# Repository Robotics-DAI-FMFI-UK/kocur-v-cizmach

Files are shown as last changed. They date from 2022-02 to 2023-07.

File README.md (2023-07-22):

# kocur-v-cizmach
Cat-like arduino robot with 4 legs

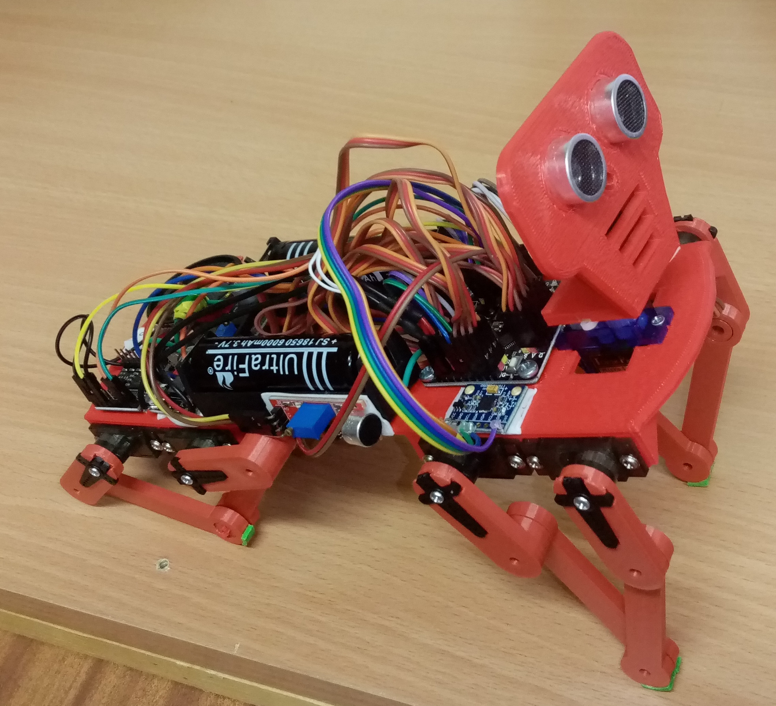
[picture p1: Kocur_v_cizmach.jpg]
kocúr v čižmách


list of parts:

mechanical:

* 4 legs - each made of 4 different pieces
* main body
* head
* screws for fixing arduino, power supply, and battery holders

electronic:

* 2x plastic holder for 16500 LiIon batteries
* 2x 16500 LiIon batteries
* 8x mg90s servo + 1x sg90 or mg90 for head (or 1x continuous servo for new version with rotating front legs)
* arduino nano strong
* lm2596 tuned to 5V (or 2x 5V4A step-down regulator)
* HC-SR04 ultrasonic sensor
* passive buzzer
* KCD-11 power switch
* cables
* resistor divider (i.e. 5.5K + 56K) to measure bat. voltage

optional:

* HC-05 compatible BT module
* extra 5V4A power supply to avoid spurious resets
* DfPlayer Mini, 2W 8Ohm speaker and microSD card
* analog microphone
* mpu6050 gyro/accelerometer
* capacitance touch sensor

Pin connections:

    D0   reserved for programming/serial comm on USB 
    D1   reserved for programming/serial comm on USB 
    D2   BT Tx (i.e. our Rx, signal from BT to Arduino)
    D3   Right back 2 (RB2)
    D4   BT Rx (i.e. our Tx, signal from Arduino to BT)
    D5   Right back 1 (RB1)
    D6   Right front 2 (RF2)
    D7   Right front 1 (RF1)
    D8   Left front 2 (LF2)
    D9   Left front 1 (LF1)
    D10  Left back 1 (LB1)
    D11  Left back 2 (LB2)
    D12  Head
    D13  Buzzer
    A0   US Trig
    A1   US Echo
    A2   DfPlayer Mini Rx
    A3   voltage divider on batteries
    A4   SDA of MPU6050
    A5   SCL of MPU6050
    A6   Touch sensor
    A7   Microphone

Building instructions: https://kempelen.dai.fmph.uniba.sk/files/kocur-v-cizmach-manual/

Choreographies are sequences of motor angles 0-179 8-tuples in this order: (delay is in ms and is applied 100-times per each move, typical values 1-10, e.g. 1 => the movement is spread over 100 steps, each lasting 1ms, in total about 100 ms. To change that parameter, edit play_step() function)

    LF1 LB1 RF1 RB1 LF2 LB2 RF2 RB2 delay

In edit mode, use the following keys to move all degrees of freedom:

   (-> means forward, <- means backward, servo 1 is front, servo 2 back)

    1  LF1 -> -      2  LB1 -> -      3  RF1 -> +      4  RB1 -> +
    q  LF1 <- +      w  LB1 <- +      e  RF1 <- -      r  RB1 <- -
    a  LF2 <- +      s  LB2 -> -      d  RF2 <- -      f  RB2 -> +
    z  LF2 -> -      x  LB2 <- +      c  RF2 -> +      v  RB2 <- -

Kocúr v čižmách (https://www.youtube.com/watch?v=T9AiIFP-OWI)

https://www.youtube.com/watch?v=T9AiIFP-OWI

https://youtu.be/DKM0F1i9IDY

Software:

Arduino program allows to work with "choreographies": create, edit, test and debug, import, export, store into EEPROM, setup autoplay, and control the attached gadgets over the cable or Bluetooth module. Each of the three modes has interactive control and 'h' shows help - list of available commands:

    MoKraRoSA. Press H for help
    Control mode. Hit E for edit mode.
     1: forward
     2: backward
     3: right
     4: left
     5: down
     6: sit
     7: look around
    Play the sequence: /
    Repetitive play: \
    Play eeprom seq: t g b
    Initial position: *
    Position 90: 9
    Ultrasonic ON/OFF: u
    Battery level (*100 V): B
    Play melody: . , ; ' [ ]
    Stop melody: ESC/:
    Play/change music: m j n
    Music volume on/off: M
    Change music volume: < >
    Print help: h
    ---------------------    
    Edit mode. Hit C for control mode.
    Servo control:
    1 ... q
    2 ... w
    e ... 3
    r ... 4
    z ... a
    s ... x
    d ... c
    v ... f
    Step size control:
    - ... +
    Store next point: ENTER/W
    Print the sequence: SPACE/N
    Load (paste in) the sequence: L
    Save to EEPROM: E
    Load from EEPROM: O
    Toggle autostart: A
    Erase sequence: R
    Undo to last saved position: U
    Enter debug mode: TAB/T
    (to insert a break, repeat the same position again with delay)
    Play the sequence: /
    Repetitive play: \
    Play eeprom seq: t g b
    Initial position: *
    Position 90: 9
    Ultrasonic ON/OFF: u
    Battery level (*100 V): B
    Play melody: . , ; ' [ ]
    Stop melody: ESC/:
    Play/change music: m j n
    Music volume on/off: M
    Change music volume: < >
    Print help: h
    ---------------------    
    Debug mode:
     TAB/T   - leave debug mode
     SPACE/N - move to next step
     ENTER/W - replace with current
     ESC/:   - restore current step
     D       - delete current step
     ESC/:   - insert step before current
    Servo control:
    1 ... q
    2 ... w
    e ... 3
    r ... 4
    z ... a
    s ... x
    d ... c
    v ... f
    Step size control:
    - ... +
    Print help: h

Warning:

The LiIon batteries are sensitive to a complete discharge, therefore
the battery voltage is permanently measured using a voltage-divider
against the built-in 1.1V power regulator, and when they reach
a critical level, all functionality stops and an alarm is played
using the passive buzzer. It is recommended to recharge batteries
after the use, and store them for longer term charged to about a half
of their capacity.

Links:

*  Original project that inspired us: Baby “MIT Cheetah” opensource and 3D-printable robot by Marco (https://www.personalrobots.biz/baby-mit-cheetah-opensource-and-3d-printable-robot/)
* Our modifications in TinkerCAD (they may change): body and head (https://www.tinkercad.com/things/c9znID17vLj-cheetah-telo), legs (https://www.tinkercad.com/things/6ybUZ9S300i-cheetah-noha)
* Student project summer 2021: https://dai.fmph.uniba.sk/courses/dtv/index.php/Cheetah
* Student project winter 2021: https://wiki.robotika.sk/robowiki/index.php?title=Kocur_v_Cizmach_-_Alja%C5%BE_Andol%C5%A1ek_and_Ursek_Slivsek

contact: Pavel, pavel.petrovic at uniba.sk

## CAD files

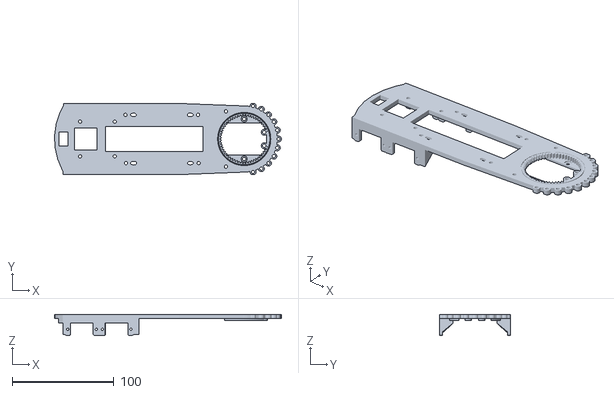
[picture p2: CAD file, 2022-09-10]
stl/v3/cheetah_v3_body_main.stl
223.0 x 70.0 x 20.8

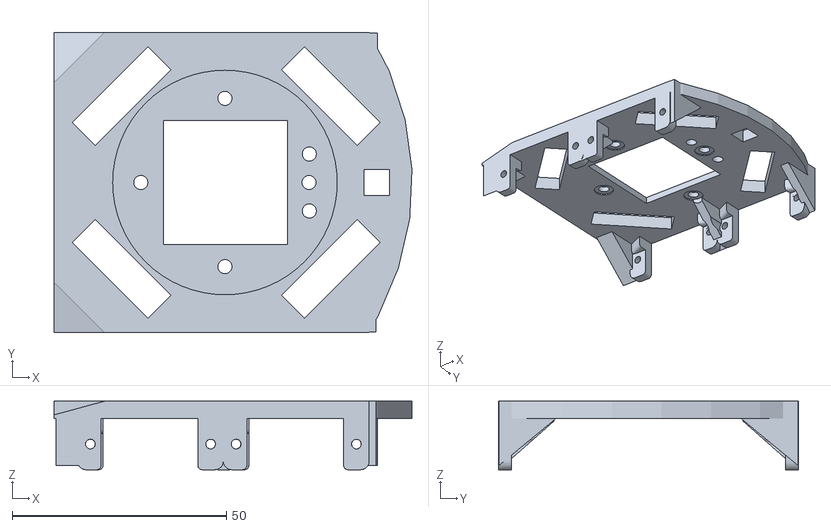
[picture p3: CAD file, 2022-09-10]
stl/v3/cheetah_v3_body_frontlegs_holder.stl
83.5 x 70.0 x 16.0

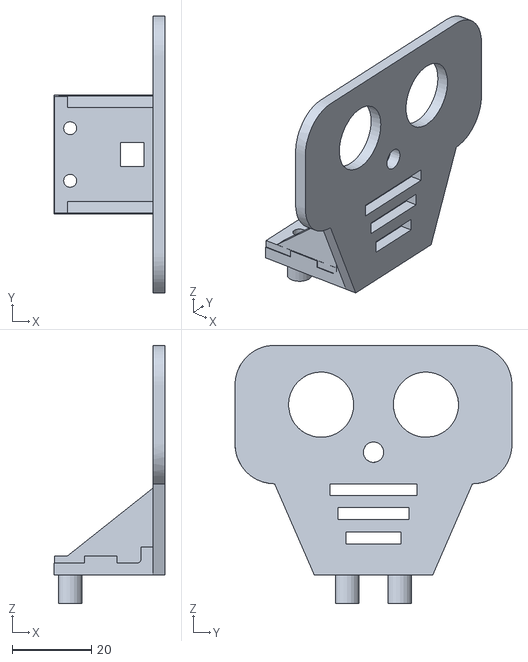
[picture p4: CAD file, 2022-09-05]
stl/v3/cheetah_v3_head.stl
28.0 x 70.0 x 65.3

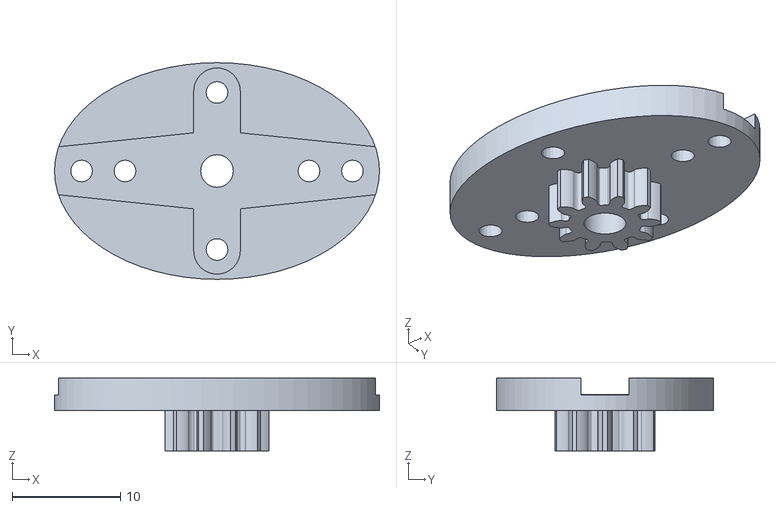
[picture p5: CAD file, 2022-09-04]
stl/v3/cheetah_v3_servo_gear.stl
30.0 x 20.0 x 6.72

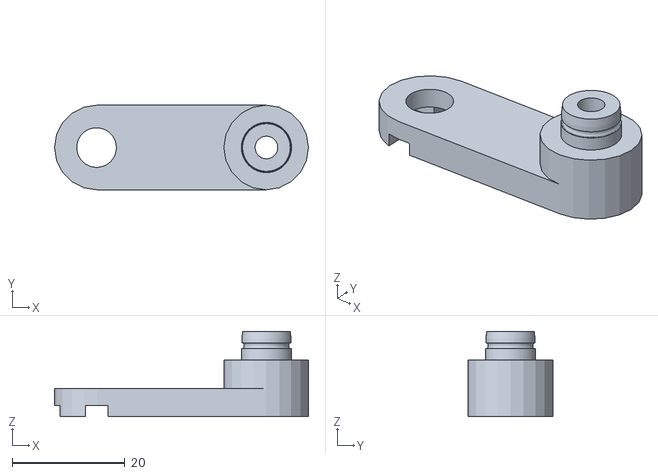
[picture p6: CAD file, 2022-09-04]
stl/v3/cheetah_v3_leg_B.stl
45.0 x 15.0 x 15.1

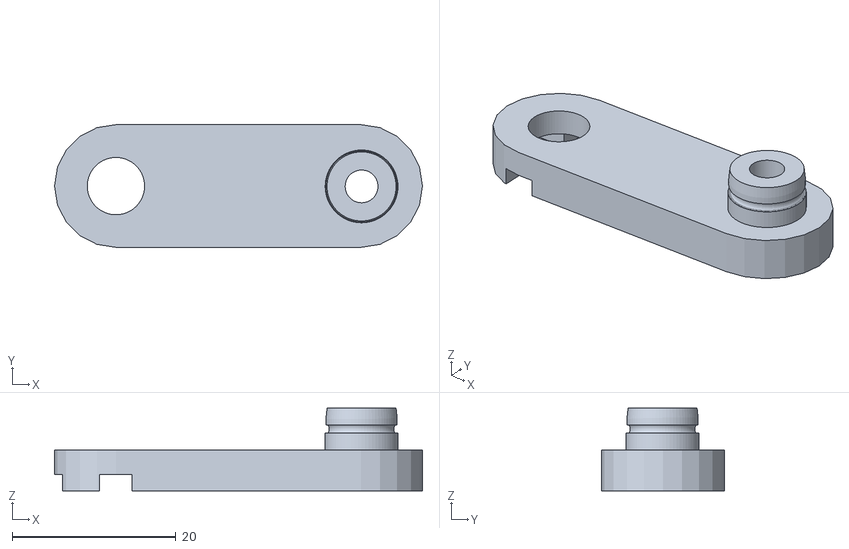
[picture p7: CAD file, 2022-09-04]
stl/v3/cheetah_v3_leg_C.stl
45.0 x 15.0 x 10.1

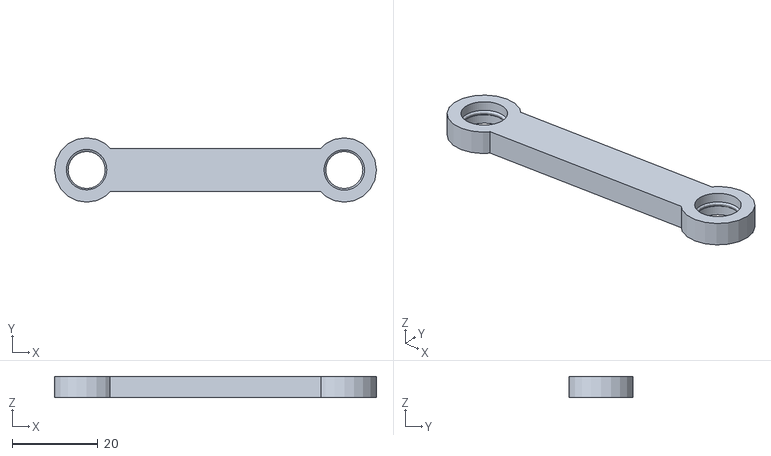
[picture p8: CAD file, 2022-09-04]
stl/v3/cheetah_v3_leg_A.stl
75.0 x 15.0 x 5.00

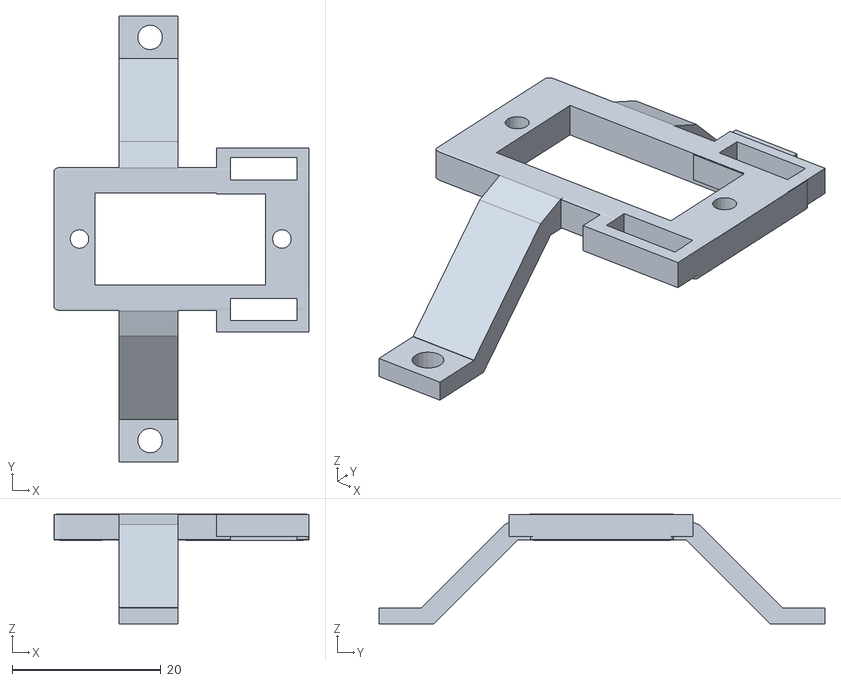
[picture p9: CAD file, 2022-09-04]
stl/v3/cheetah_v3_servo_bracket.stl
34.3 x 60.0 x 14.8

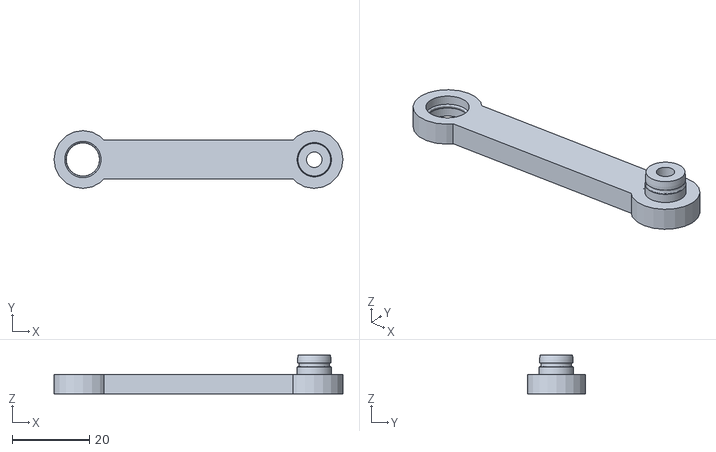
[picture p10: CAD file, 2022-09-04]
stl/v3/cheetah_v3_leg_D.stl
75.0 x 15.0 x 10.1

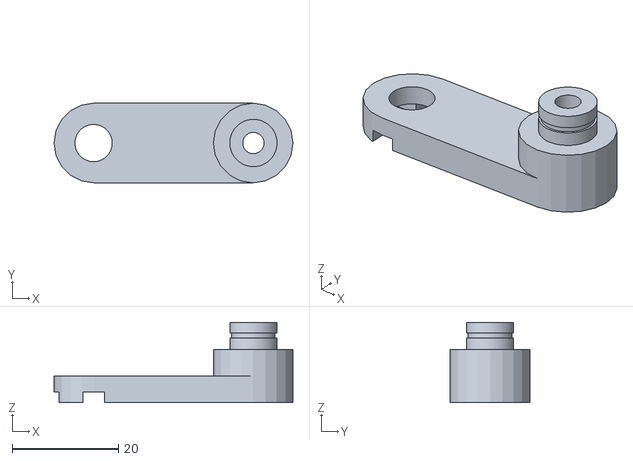
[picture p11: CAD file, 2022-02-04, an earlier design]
stl/v2/cheetah_leg_part2.stl
45.0 x 15.0 x 15.1

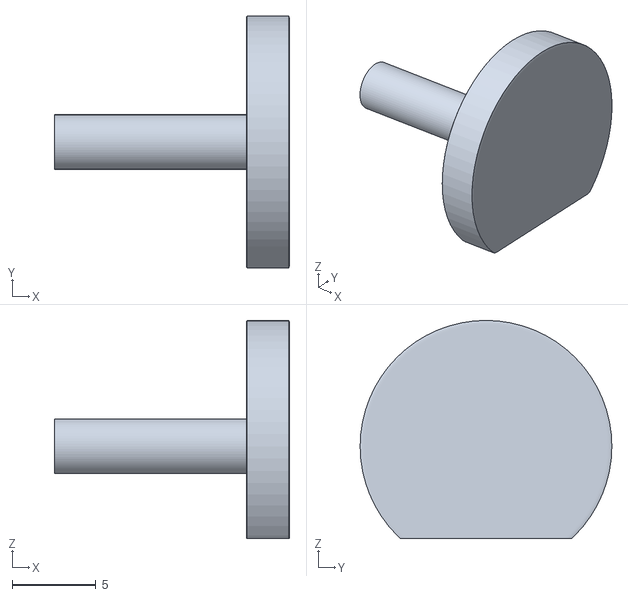
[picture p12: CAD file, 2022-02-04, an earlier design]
stl/v2/cheetah_leg_pivot.stl
14.0 x 15.0 x 13.0

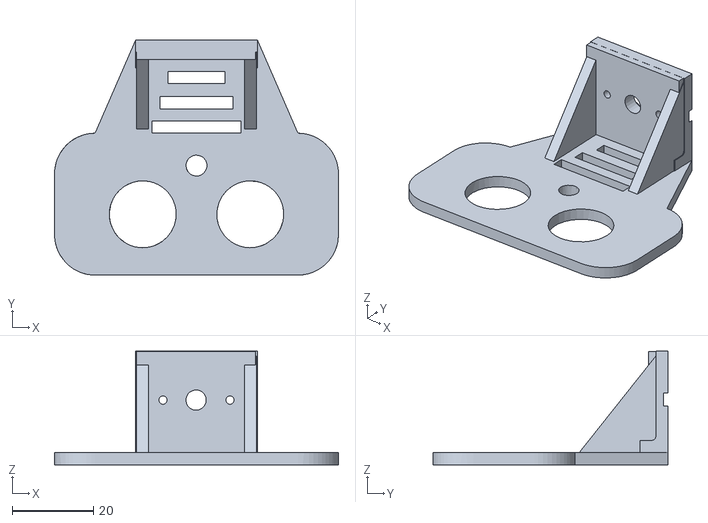
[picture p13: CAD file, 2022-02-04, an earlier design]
stl/v2/cheetah_head.stl
70.0 x 58.0 x 28.0

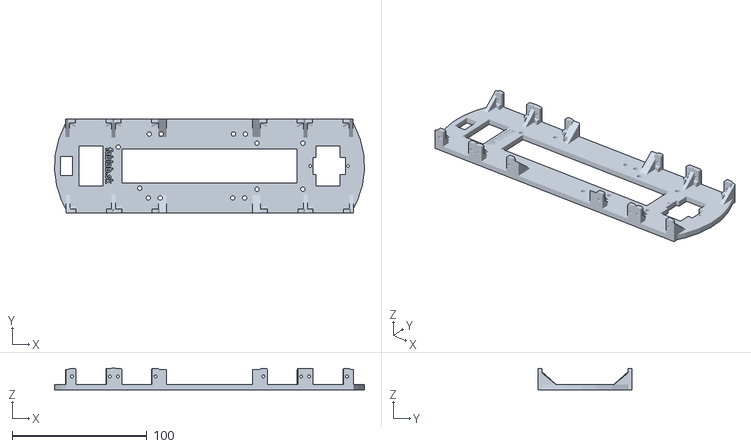
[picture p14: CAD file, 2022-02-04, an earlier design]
stl/v2/cheetah_body.stl
230.0 x 70.0 x 16.2

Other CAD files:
stl/v2/cheetah_leg_part3.stl
stl/v2/cheetah_leg_part4.stl
stl/v2/cheetah_leg_part1.stl

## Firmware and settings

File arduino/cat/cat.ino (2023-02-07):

#include <EEPROM.h>
#include <Servo.h>
#include <Wire.h>
//#include <MPU6050.h>

// put next line after comment, if you have no MPU6050 gyroscope
 //#define HAVE_GYRO

// for version 1 comment-out the following line
// #define GYRO_UPSIDE_DOWN

// put next line after comment, if you have no HC-SR04 ultrasonic 
 #define HAVE_ULTRASONIC

// pin connections:
// servos:
//    D3   Right back 2 (RB2)
//    D5   Right back 1 (RB1)
//    D6   Right front 2 (RF2)
//    D7   Right front 1 (RF1)
//    D8   Left front 2 (LF2)
//    D9   Left front 1 (LF1)
//    D10  Left back 1 (LB1)
//    D11  Left back 2 (LB2)
// bluetooth:
//    BT TX:  D2
//    BT RX:  D4
// sirene:
//    +: D13
// touch:
//    1: A6
//    2: A7
// mp3 player:
//    RX:     A2
// ultrasonic HC-SR04
//    TRIG:   A0
//    ECHO:   A1
// gyro (MPU-6050)
//    SDA:    A4
//    SCL:    A5
// battery voltage:
//    Vbat:   A3

#define MP3_OUTPUT_PIN 16   // connect Rx pin of DFPlayer to A2

#define TRIG 14    // pin A0
#define ECHO 15    // pin A1

#define SERIAL_STATE_IDLE      0
#define SERIAL_STATE_RECEIVING 1
#define SERIAL_BUFFER_LENGTH   20

// left/right front/back 1=upper, 2=lower
// LF1, LB1, RF1, RB1, LF2, LB2, RF2, RB2

#define LF1 0
#define LB1 1
#define RF1 2
#define RB1 3
#define LF2 4
#define LB2 5
#define RF2 6
#define RB2 7

#define MAX_SEQ_LENGTH 36
#define MAX_PROG_SIZE (MAX_SEQ_LENGTH * 9 + 2)

#define WARN_LED 13

Servo legs[8];
Servo head;

uint8_t legv[8];
char pluskey[] = {'q', 'w', '3', '4', 'a', 'x', 'c', 'f'};
char minuskey[] = {'1', '2', 'e', 'r', 'z', 's', 'd', 'v'};
char key_step_plus = '+';
char key_step_minus = '-';
int8_t step_size;
int seq_length;
uint8_t seq[MAX_SEQ_LENGTH][8];
uint8_t delaj[MAX_SEQ_LENGTH];
uint8_t del = 0;
uint8_t ultrasonic = 0;
uint8_t quiet = 0;
uint8_t upside_down = 0;
int pitch;
int roll;
uint8_t current_song = 1;
uint8_t volume;
uint8_t head_position = 90;


uint8_t usb_active;
uint8_t bt_active;

uint8_t in_edit_mode;
uint8_t debug_mode;
uint8_t debugged_step;

uint8_t initial[] = {90,90,90,90,90,90,90,90};

uint8_t australian[] = {45,135,135,45,5,175,175,5};

// #ifdef HAVE_GYRO
//MPU6050 mpu;
// #endif

int usual_delay = 70;
int inp = 0;
int8_t laying = 0;
int auto_cube = 0;
int auto_safe = 0;
int safe_delay = 500;

static volatile uint8_t serial_state;
static uint8_t serial_buffer[SERIAL_BUFFER_LENGTH];
static volatile uint8_t serial_buf_wp, serial_buf_rp;

static volatile uint8_t receiving_byte;

static volatile uint32_t time_startbit_noticed;
static volatile uint8_t next_bit_order;
static volatile uint8_t waiting_stop_bit;
static uint16_t one_byte_duration;
static uint16_t one_bit_duration;
static uint16_t one_bit_write_duration;
static uint16_t half_of_one_bit_duration;
static uint8_t ignore_batteries = 0;
static volatile int touch;

//------------------------- place your reactions code here --------------------
void react_to_gyro()
{
  refresh_gyro();
  // your code here
}

void react_to_multitouch(uint8_t num_touches)
{
    switch (num_touches)
    {
      case 2: //double-touch
              down_to_earth();
              break;
      case 3: //tripple-touch
              sit_down();
              break;
      case 4: //quadruple-touch
              reset_position();
              break;
      case 5: //5-touches :-)
              forward();
              break;
      case 6: //6-touches :-)
              backward();
              break;
      case 7: //happy 7-touches
              left();
              break;
      case 8: //gothic 8 touches   
              right();
              break;    
      case 9: //epic 9 touches switch ultrasonic
              ultrasonic = 1 - ultrasonic;
              break;                
      case 10: //tenth finger moves the head
              //move_head();
              break;                
    }
}

void react_to_touch()
{
  if (quiet) toggle_quiet();
  mp3_play(current_song);
}

void react_to_tap()
{
  toggle_quiet();
}

void react_to_mic()
{
  //move_head();
  forward();
}
//----------------------------------- end of reactions code --------------------------------

void setup() 
{
  usb_active = 0;
  bt_active = 0;
  in_edit_mode = 0;
  debug_mode = 0;
  volume = 20;
  seq_length = 0;
  
  legs[LB2].attach(11);
  legs[LB1].attach(10);
  legs[LF2].attach(8);
  legs[LF1].attach(9);
  legs[RB2].attach(3);
  legs[RB1].attach(5);
  legs[RF2].attach(6);
  legs[RF1].attach(7);
  head.attach(12);
  reset_position();

  pinMode(WARN_LED, OUTPUT);
  digitalWrite(WARN_LED, LOW);
  pinMode(TRIG, OUTPUT);
  pinMode(ECHO, INPUT);
  Serial.begin(9600);
  init_tone2();

  // configure ADC
  ADMUX = 0b01000011;
  ADCSRA = 0b10010101;
  ADCSRB = 0;
  DIDR0 = 8;  // disable A3 digital

  while (Serial.available()) Serial.read();
  Serial.println(F("Hi! Press U for USB-powered run."));
  delay(2500);
  if (Serial.available())
  {
    if (Serial.read() == 'U') 
    {
      ignore_batteries = 1;
      Serial.println(F("USB-powered"));
    }
    usb_active = 1;
  }
  else Serial.println(F("Bat.powered"));
  Serial.println(F("MoKraRoSA. Press H for help"));
  init_serial(9600);
  
// #ifdef HAVE_GYRO
//  mpu.begin(MPU6050_SCALE_2000DPS, MPU6050_RANGE_2G);
// #endif

  step_size = 1;
  sound_greeting();
    
  mp3_set_volume(volume);
  
  if (load_autostart()) play_sequence(1);
}

void sound_greeting()
{
  tone2(440, 50);
  delay(50);
  tone2(880, 100);
  delay(100);
  tone2(1760, 50);
  delay(50);
}

void position_90()
{
    for (int i = 0; i < 8; i++)
      legv[i] = 90;
       
    for (int i = 0; i < 8; i++)
      legs[i].write(legv[i]);
}

void reset_position()
{
    for (int i = 0; i < 8; i++)
      legv[i] = initial[i];
       
    for (int i = 0; i < 8; i++)
      legs[i].write(legv[i]);
      
    head.write(90);
}

// walking
const uint8_t len_fwdwalk = 15;
const uint8_t fwdwalk[] PROGMEM = {  75,75,105,105,105,105,75,75,1,
                                     100,100,80,80,135,135,45,45,1,
                                     70,90,100,80,165,145,25,45,1,
                                     70,90,100,110,165,145,25,15,1,
                                     70,90,100,145,165,145,25,90,1,
                                     100,100,80,145,135,135,45,90,1,
                                     100,100,90,145,135,135,35,90,1,
                                     100,70,90,145,135,165,35,90,1,
                                     100,40,90,145,135,90,35,90,1,
                                     75,40,90,155,160,90,35,90,1,
                                     45,40,90,155,90,90,35,90,1,
                                     45,40,90,125,90,90,60,90,1,
                                     45,25,90,135,90,105,60,80,1,
                                     45,25,120,135,90,105,30,80,1,
                                     45,25,150,135,90,105,90,80,1 };
                                     
void walk_from_memory(uint8_t dir, uint8_t *mem, int len)
{      
    int st[9];   
    uint8_t stop_walking = 0;
   
    do {
      char *m = mem;
      if (dir == 0) m += (len * 9 - 9);
      
      for (int i = 0; i < len; i++)
      {
        if (Serial.available()) { stop_walking = 1; break; }
        if (serial_available()) { stop_walking = 1; break; }
        read_touch();
        if (touch > 500) { stop_walking = 1; break; }
          
        for (int j = 0; j < 9; j++)
        {
          st[j] = (int)pgm_read_byte(m++);          
        }
        if (dir == 0) m -= 18;
      
        for (int k = 0; k < 100; k++)
        {
          for (int j = 0; j < 8; j++)        
             legs[j].write(legv[j] + ((int)(st[j] - legv[j]) * k) / 100);      
          delay(st[8]);
        }
        for (int j = 0; j < 8; j++)        
          legv[j] = st[j];
                
        check_battery();
      }
    } while (!stop_walking);
    
    while (Serial.available()) Serial.read();
    while (serial_available()) serial_read(); 
    while (touch > 500) { read_touch();}
}

void forward()
{  
  walk_from_memory(1, fwdwalk, len_fwdwalk);
}

void backward()
{
  walk_from_memory(0, fwdwalk, len_fwdwalk);
}

const uint8_t len_turnwalk = 5;
const uint8_t turnleft[] PROGMEM = { 90,41,130,108,90,126,134,65,5,
                                     35,77,130,128,80,126,134,32,5,
                                     19,77,130,152,80,130,134,128,5,
                                     43,39,163,139,30,21,165,84,5,
                                     90,90,90,90,90,90,90,90,5 };

const uint8_t turnright[] PROGMEM = { 50, 72, 90, 139, 46, 115, 90, 54, 5,
                                     50, 52, 145, 103, 46, 148, 100, 54, 5,
                                     50, 28, 161, 103, 46, 52, 100, 50, 5,                                     
                                     17, 12, 137, 141, 15, 117, 150, 159, 5,
                                     90,90,90,90,90,90,90,90,5 };

void right()
{
  walk_from_memory(1, turnright, len_turnwalk);
}

void left()
{
  walk_from_memory(1, turnleft, len_turnwalk);  
}

const uint8_t position_down[] = { 5, 5, 175, 175, 175, 175, 5, 5 };
const uint8_t position_sit[] = { 90, 5, 90, 175, 90, 175, 90, 5 };

void position_from_memory(const uint8_t *m)
{  
  for (int k = 0; k < 100; k++)
  {
    for (int j = 0; j < 8; j++)        
       legs[j].write(legv[j] + ((int)(m[j] - legv[j]) * k) / 100);
    delay(3);
  }
  for (int j = 0; j < 8; j++)        
     legv[j] = m[j];  
}

void down_to_earth()
{  
  position_from_memory(position_down);
}

void sit_down()
{
  position_from_memory(position_sit);
}

char read_latest_char() 
{
  char c = 0;
  while (serial_available() > 0)
    c = serial_read();
  return c;
}

void refresh_gyro()
{
#ifdef HAVE_GYRO
//  Vector normAccel = mpu.readNormalizeAccel();
//  pitch = -(atan2(normAccel.XAxis, sqrt(normAccel.YAxis*normAccel.YAxis + normAccel.ZAxis*normAccel.ZAxis))*180.0)/M_PI;
//  roll = (atan2(normAccel.YAxis, normAccel.ZAxis)*180.0)/M_PI;  
#ifdef GYRO_UPSIDE_DOWN
  roll += 180;
  if (roll > 180) roll -= 360;
#endif
#endif
}

void toggle_quiet()
{
    if (quiet) mp3_set_volume(volume);
    else mp3_set_volume(0);   
    serial_print_flash(PSTR("music:"));
    serial_println_num(quiet);
    quiet = 1 - quiet;  
}

void both_modes(char c)
{
  if (c == '/')
    play_sequence(0);
  else if (c == '\\')
    play_sequence(1);
  else if (c == 't'){
    if (load_from_EEPROM(1))
      play_sequence(1);
  }
  else if (c == 'g'){
    if (load_from_EEPROM(2))
      play_sequence(1);
  }
  else if (c == 'b'){
    if (load_from_EEPROM(3))
      play_sequence(1);
  }
  else if (c == '*')
  {
    reset_position();
    laying = 0;
  }
  else if (c == '9')
    position_90();
  else if (c == 'M')
  {
    toggle_quiet();
  }
  else if ((c == 27) || (c == ':')) stop_melody();
  else if ((c == '<') || (c == '>'))
  {
    if (c == '<') { if (volume > 0) volume--; }
    else if (volume < 30) volume++;
    mp3_set_volume(volume);
    serial_print_flash(PSTR("vol: "));
    serial_println_num(volume);
  }
  else if (c == 'u')
  {
    ultrasonic = 1 - ultrasonic;
    serial_print_flash(PSTR("ultra:"));
    serial_println_num(ultrasonic);
  }
  else if ((c == 'h') || (c == 'H') || (c == '?')) print_usage();
  else if (c == 'B') serial_println_num(measure_bat());
  else try_melodies(c);
}
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
void loop() 
{
  check_mic();
  check_touch();
  
#ifdef HAVE_ULTRASONIC
  if ((measure_US() < 15) && ultrasonic)
  {
    // insert your code to react to obstacle in front of robot here
    backward();
  }
#endif

  if (serial_available()) control_over_bt();
  if (Serial.available()) control_over_serial();
  
  pitch = 0;
  roll = 0;
#ifdef HAVE_GYRO
  react_to_gyro();
#endif

  check_battery();
}

void print_usage()
{
  if (in_edit_mode)
  {
    if (debug_mode)
    {
      serial_println_flash(PSTR("Debug mode:"));
      serial_println_flash(PSTR(" TAB/T   - leave debug mode"));
      serial_println_flash(PSTR(" SPACE/N - move to next step"));
      serial_println_flash(PSTR(" ENTER/W - replace with current"));
      serial_println_flash(PSTR(" ESC/:   - restore current step"));
      serial_println_flash(PSTR(" D       - delete current step"));
      serial_println_flash(PSTR(" ESC/:   - insert step before current"));
    }
    else serial_println_flash(PSTR("Edit mode. Hit C for control mode."));
    serial_println_flash(PSTR("Servo control:"));
    for (int i = 0; i < 8; i++)
    {
      serial_print_char(minuskey[i]);
      serial_print_flash(PSTR(" ... "));
      serial_println_char(pluskey[i]);
    }
    serial_println_flash(PSTR("Step size control:"));
    serial_print_char(key_step_minus);
    serial_print_flash(PSTR(" ... "));
    serial_println_char(key_step_plus);
    delay(150);
    if (!debug_mode)
    {
      serial_println_flash(PSTR("Store next point: ENTER/W"));
      serial_println_flash(PSTR("Print the sequence: SPACE/N"));
      serial_println_flash(PSTR("Load (paste in) the sequence: L"));
      serial_println_flash(PSTR("Save to EEPROM: E"));
      serial_println_flash(PSTR("Load from EEPROM: O"));
      serial_println_flash(PSTR("Toggle autostart: A"));
      serial_println_flash(PSTR("Erase sequence: R"));
      serial_println_flash(PSTR("Undo to last saved position: U"));
      serial_println_flash(PSTR("Enter debug mode: TAB/T"));
      serial_println_flash(PSTR("(to insert a break, repeat the same position again with delay)"));   
    }
    else
    {
      serial_println_flash(PSTR("Print help: h"));
      return;
    }
  } else
  {   
    serial_println_flash(PSTR("Control mode. Hit E for edit mode."));    
    serial_println_flash(PSTR(" 1: forward"));
    serial_println_flash(PSTR(" 2: backward"));
    serial_println_flash(PSTR(" 3: right"));
    serial_println_flash(PSTR(" 4: left"));
    serial_println_flash(PSTR(" 5: down"));
    serial_println_flash(PSTR(" 6: sit"));
    serial_println_flash(PSTR(" 7: look around"));
    //serial_println_flash(PSTR(" 8: your option here"));  
    //serial_println_flash(PSTR(" 0: your option here"));
  } 
  delay(150); 
  serial_println_flash(PSTR("Play the sequence: /"));
  serial_println_flash(PSTR("Repetitive play: \\"));
  serial_println_flash(PSTR("Play eeprom seq: t g b"));
  serial_println_flash(PSTR("Initial position: *"));
  serial_println_flash(PSTR("Position 90: 9"));
  serial_println_flash(PSTR("Ultrasonic ON/OFF: u"));
  serial_println_flash(PSTR("Battery level (*100 V): B"));
  serial_println_flash(PSTR("Play melody: . , ; ' [ ]"));
  serial_println_flash(PSTR("Stop melody: ESC/:"));
  delay(150); 
  serial_println_flash(PSTR("Play/change music: m j n"));
  serial_println_flash(PSTR("Music volume on/off: M"));
  serial_println_flash(PSTR("Change music volume: < >"));
  serial_println_flash(PSTR("Print help: h"));
}

void store_new_point()
{
  char c = 0;
  if (seq_length == MAX_SEQ_LENGTH) return;
  while ((c != 13) && (c != 'W'))
  {
    serial_print_flash(PSTR(" "));
    serial_print_char((char)13);
    serial_print_flash(PSTR("(+/-/ENTER;W) delay = "));
    serial_print_num(del);
    while ((!Serial.available()) && !serial_available());
    if (Serial.available()) c = Serial.read();
    else c = serial_read();
    if (c == '+') if (del < 30) del++;
    if (c == '-') if (del > 0) del--;
  }
  serial_println();
  for (int i = 0; i < 8; i++)
    seq[seq_length][i] = legv[i];
  delaj[seq_length] = del;
  dump_row(seq_length);
  seq_length++;
}

void dump_row(int i)
{
    for (int j = 0; j < 8; j++)
    {
      serial_print_num(seq[i][j]);
      serial_print_flash(PSTR(" "));
    }
    serial_println_num(delaj[i]);
}

void dump_sequence(uint8_t step_numbers)
{
  serial_println_flash(PSTR("---"));
  for (int i = 0; i < seq_length; i++)
  {
    if (step_numbers) 
    { 
       serial_print_num(i);
       serial_print_flash(PSTR(". "));
    }
    dump_row(i);
  }
  serial_println_flash(PSTR("---"));
}

void play_step(uint8_t i)
{
   uint8_t index_new = i;
   uint8_t index_old = i - 1;
   if (i == 0) index_old = seq_length - 1;
      
   if (delaj[index_new] == 0)
   for (int j = 0; j < 8; j++)
      legs[j].write(seq[index_new][j]);
   else for (int k = 0; k < 100; k++)
   {
      for (int j = 0; j < 8; j++)        
         legs[j].write(seq[index_old][j] + ((int)(seq[index_new][j] - seq[index_old][j]) * k) / 100);
      delay(delaj[index_new]);
   } 
}

void play_sequence(uint8_t repete)
{
  if (repete) if (!quiet) play_melody(6);
  do 
  {
    for (int i = 0; i < seq_length; i++)
    {      
      if (Serial.available()) { Serial.read(); repete = 0; break; }
      if (serial_available()) { serial_read(); repete = 0; break; }
      dump_row(i);
      read_touch();
      if (touch > 500) break;
      play_step(i);
      check_battery();      
    }
    if (Serial.available()) { Serial.read(); break; }
    if (serial_available()) { serial_read(); break; }
    if (touch > 500) break;
  } while (repete);
  for (int i = 0; i < 8; i++)
    legv[i] = seq[seq_length - 1][i];
  stop_melody();
  while (touch > 500) read_touch();
}

void load_sequence()
{
  // init
  serial_print_flash(PSTR("Paste the sequence (or type SPACE/N to cancel): "));
  char c;
  uint8_t ok;
  
  // idk
  do {
    c = serial_peek();
  } while (c == -1);
  
  // check if cancelled
  if ((c == ' ')  || (c == 'N'))
  {
    Serial.read();
    serial_println_flash(PSTR("cancelled."));
    return;
  }

  // reset seq_length
  seq_length = 0;
  serial_println();
  serial_println_flash(PSTR("loading... (terminate with empty line)"));

  // while true read and write
  do {
    while ((!Serial.available()) && !serial_available());
    c = serial_peek();
    if ((c == 'k') || (c == 10) || (c == 13)) break;
    ok = 1;
    for (int i = 0; ok & (i < 8); i++) 
    {
       seq[seq_length][i] = read_number(&ok);    
      if (!ok) break;   
    }    
    delaj[seq_length] = read_number(&ok);
    
    if (!ok) break;
    
    serial_println();
    seq_length++;
  } while (1);

  // check status
  if (!ok)
    serial_println_flash(PSTR("Failed."));
  else
    serial_println_flash(PSTR("Done."));
  while (Serial.available()) Serial.read();
  while (serial_available()) serial_read();
}

int read_number(uint8_t *ok)
{
    int x = 0;
    *ok = 0;
    while (1) {
    if (Serial.available() || serial_available())
    {
      int c;
      if (Serial.available()) c = Serial.read();
      else c = serial_read();
      serial_print_char(c);
      if (c == 8) x /= 10;
      if ((c >= '0') && (c <= '9'))
      {
        *ok = 1;
        x = x * 10 + (c - '0');
      } else return x;
    }
  }
}

void dump_state()
{
    for (int j = 0; j < 8; j++)
    {
      serial_print_num(legv[j]);
      serial_print_flash(PSTR(" "));
    }
    serial_println();
}

void undo_step()
{
  uint8_t changed = 0;
  if (seq_length > 0)
  {
    for (int i = 0; i < 8; i++)
      if (seq[seq_length - 1][i] != legv[i]) changed = 1;
  }
  else
  {
    for (int i = 0; i < 8; i++)
    {
      legv[i] = initial[i];
      legs[i].write(legv[i]);
    } 
    return;
  }
  
  if (!changed)
  {
    if (seq_length == 0)
    {
      serial_println_flash(PSTR("Nothing to undo."));
      return; 
    }
    serial_print_flash(PSTR("Nothing changed, erase last saved step? [y/n]: "));
    char c = anyserial_readchar();
    if (c != 'y') return;
    seq_length--; 
    serial_println_flash(PSTR("erased."));
  }
  else
  {
    serial_print_flash(PSTR("Undo? [y/n]: "));
    char c = anyserial_readchar();
    if (c == 'n') return;
  }
  if (seq_length > 0)
    for (int i = 0; i < 8; i++)
    {
      legv[i] = seq[seq_length - 1][i];
      legs[i].write(legv[i]);
    }
  else reset_position();
}

int8_t ask_for_slot_num()
{
  serial_print_flash(PSTR("Seq.slot 1-3: "));
  char c = anyserial_readchar();
  if ((c < '1') || (c > '3')) 
  {
    serial_println_flash(PSTR("range is 1-3"));
    return -1;
  }
  return c - '1';
}

char anyserial_readchar()
{
  char c;
  while ((!Serial.available()) && !serial_available());
  if (Serial.available()) c = Serial.read();
  else c = serial_read();
  serial_println_char(c);
  return c;
}
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

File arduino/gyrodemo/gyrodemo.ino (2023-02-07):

// I2Cdev and MPU6050 must be installed as libraries, or else the .cpp/.h files
// for both classes must be in the include path of your project
#include "I2Cdev.h"

#include "MPU6050_6Axis_MotionApps612.h"
//#include "MPU6050.h" // not necessary if using MotionApps include file

// Arduino Wire library is required if I2Cdev I2CDEV_ARDUINO_WIRE implementation
// is used in I2Cdev.h
#if I2CDEV_IMPLEMENTATION == I2CDEV_ARDUINO_WIRE
#include "Wire.h"
#endif

// class default I2C address is 0x68
// specific I2C addresses may be passed as a parameter here
// AD0 low = 0x68 (default for SparkFun breakout and InvenSense evaluation board)
// AD0 high = 0x69
MPU6050 mpu;
//MPU6050 mpu(0x69); // <-- use for AD0 high



#define INTERRUPT_PIN 2  // use pin 2 on Arduino Uno & most boards
#define LED_PIN 13 // (Arduino is 13, Teensy is 11, Teensy++ is 6)
bool blinkState = false;

// MPU control/status vars
bool dmpReady = false;  // set true if DMP init was successful
uint8_t mpuIntStatus;   // holds actual interrupt status byte from MPU
uint8_t devStatus;      // return status after each device operation (0 = success, !0 = error)
uint16_t packetSize;    // expected DMP packet size (default is 42 bytes)
uint16_t fifoCount;     // count of all bytes currently in FIFO
uint8_t fifoBuffer[64]; // FIFO storage buffer

// orientation/motion vars
Quaternion q;           // [w, x, y, z]         quaternion container
VectorFloat gravity;
float ypr[3];           // [yaw, pitch, roll]   yaw/pitch/roll container and gravity vector


// ================================================================
// ===               INTERRUPT DETECTION ROUTINE                ===
// ================================================================

volatile bool mpuInterrupt = false;     // indicates whether MPU interrupt pin has gone high
void dmpDataReady() {
  mpuInterrupt = true;
}



// ================================================================
// ===                      INITIAL SETUP                       ===
// ================================================================

void setup() {
  // join I2C bus (I2Cdev library doesn't do this automatically)
#if I2CDEV_IMPLEMENTATION == I2CDEV_ARDUINO_WIRE
  Wire.begin();
  Wire.setClock(400000); // 400kHz I2C clock. Comment this line if having compilation difficulties
#elif I2CDEV_IMPLEMENTATION == I2CDEV_BUILTIN_FASTWIRE
  Fastwire::setup(400, true);
#endif

  // initialize serial communication
  // (115200 chosen because it is required for Teapot Demo output, but it's
  // really up to you depending on your project)
  Serial.begin(115200);
  while (!Serial); // wait for Leonardo enumeration, others continue immediately

  // NOTE: 8MHz or slower host processors, like the Teensy @ 3.3V or Arduino
  // Pro Mini running at 3.3V, cannot handle this baud rate reliably due to
  // the baud timing being too misaligned with processor ticks. You must use
  // 38400 or slower in these cases, or use some kind of external separate
  // crystal solution for the UART timer.

  // initialize device
  Serial.println(F("Initializing I2C devices..."));
  mpu.initialize();
  pinMode(INTERRUPT_PIN, INPUT);

  // verify connection
  Serial.println(F("Testing device connections..."));
  Serial.println(mpu.testConnection() ? F("MPU6050 connection successful") : F("MPU6050 connection failed"));

  // wait for ready
  Serial.println(F("\nSend any character to begin DMP programming and demo: "));
  while (Serial.available() && Serial.read()); // empty buffer
  while (!Serial.available());                 // wait for data
  while (Serial.available() && Serial.read()); // empty buffer again

  // load and configure the DMP
  Serial.println(F("Initializing DMP..."));
  devStatus = mpu.dmpInitialize();

  // supply your own gyro offsets here, scaled for min sensitivity
  mpu.setXGyroOffset(51);
  mpu.setYGyroOffset(8);
  mpu.setZGyroOffset(21);
  mpu.setXAccelOffset(1150);
  mpu.setYAccelOffset(-50);
  mpu.setZAccelOffset(1060);
  // make sure it worked (returns 0 if so)
  if (devStatus == 0) {
    // Calibration Time: generate offsets and calibrate our MPU6050
    mpu.CalibrateAccel(6);
    mpu.CalibrateGyro(6);
    Serial.println();
    mpu.PrintActiveOffsets();
    // turn on the DMP, now that it's ready
    Serial.println(F("Enabling DMP..."));
    mpu.setDMPEnabled(true);

    // enable Arduino interrupt detection
    Serial.print(F("Enabling interrupt detection (Arduino external interrupt "));
    Serial.print(digitalPinToInterrupt(INTERRUPT_PIN));
    Serial.println(F(")..."));
    attachInterrupt(digitalPinToInterrupt(INTERRUPT_PIN), dmpDataReady, RISING);
    mpuIntStatus = mpu.getIntStatus();

    // set our DMP Ready flag so the main loop() function knows it's okay to use it
    Serial.println(F("DMP ready! Waiting for first interrupt..."));
    dmpReady = true;

    // get expected DMP packet size for later comparison
    packetSize = mpu.dmpGetFIFOPacketSize();
  } else {
    // ERROR!
    // 1 = initial memory load failed
    // 2 = DMP configuration updates failed
    // (if it's going to break, usually the code will be 1)
    Serial.print(F("DMP Initialization failed (code "));
    Serial.print(devStatus);
    Serial.println(F(")"));
  }

  // configure LED for output
  pinMode(LED_PIN, OUTPUT);
}



// ================================================================
// ===                    MAIN PROGRAM LOOP                     ===
// ================================================================

void loop() {
  // if programming failed, don't try to do anything
  if (!dmpReady) return;
  // read a packet from FIFO
  if (mpu.dmpGetCurrentFIFOPacket(fifoBuffer)) { // Get the Latest packet 

    // display Euler angles in degrees
    mpu.dmpGetQuaternion(&q, fifoBuffer);
    mpu.dmpGetGravity(&gravity, &q);
    mpu.dmpGetYawPitchRoll(ypr, &q, &gravity);
    Serial.print("ypr\t");
    Serial.print(ypr[0] * 180 / M_PI);
    Serial.print("\t");
    Serial.print(ypr[1] * 180 / M_PI);
    Serial.print("\t");
    Serial.print(ypr[2] * 180 / M_PI);

    // blink LED to indicate activity
    blinkState = !blinkState;
    digitalWrite(LED_PIN, blinkState);
  }
}

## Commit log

2022-01-26 adding arduino code for the robot
2022-02-04 connecting sensors, hard-wiring walking
2022-02-04 adding stl files and links
    [cheetah_body.stl, cheetah_head.stl, cheetah_leg_part1.stl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]
2022-09-04 adding STLs v3 (with turnable front legs)
    [cheetah_body.stl, cheetah_head.stl, cheetah_leg_part1.stl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]
2022-09-05 head had a gap
    [cheetah_v3_head.stl]
2022-09-09 It's getting better all the time
    [cheetah_v3_body_main.stl]
2022-09-10 Add files via upload
    bigger holes for battery holder screws to allow flexibility and avoid bending of body and improving holes for servo holder screws
    [cheetah_v3_body_frontlegs_holder.stl, cheetah_v3_body_main.stl]
2023-01-30 adding simple mpu6050 demo, cat with frontlegs rotation up to LED, first version of walking with rotation
